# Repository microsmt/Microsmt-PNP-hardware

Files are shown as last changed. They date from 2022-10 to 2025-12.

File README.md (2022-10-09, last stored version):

# Microsmt-PNP-hardwware
# Introduction
  We are building hardware suitable for OPENPNP. All its functions are only for OPENPNP.
# No.1  PNP Mainboard
 1:About the pnp  mainboard The schematic diagram of microsmt pnpboard is modified from the open source document of smoothieboard, mainly as follows:

 2: The network module and temperature measurement module are deleted because they are meaningless to the PNP machine.

 3: The A5984 driver chip is replaced by the easier and cheaper TMC2209 driver module, so the electronic potentiometer MCP4451 is useless. When you need to change the drive current, you need to use a screwdriver to turn the mechanical potentiometer on the TMC2209 module.

4: 3pcs freewheeling diodes is connected in parallel to the drive mos of the vacuum pump and relay. avoid the reverse current of the motor damage the mos.

5: Some chips have been replaced with brands with the same parameters but easier to buy.

6：We do not have a separate software version. It is recommended to obtain the firmware dedicated to OPENPNP from the following link. It is contributed by makr.
                  https://makr.zone/smoothieware-new-firmware-for-pnp/500/
                  
 Notice：The  sch  and  pcb  document   only  open with  AD.
  
# No.2  PNP  Frame
 1： We used aluminum alloy profiles and laser cut aluminum plates to build a low cost but strong framework.The advantage of aluminum cutting piece is that its strength is much higher than that of 3D printing piece, and its accuracy will not be changed due to deformation
 
 2：it  can adjust the height of the platform and the height of feeder  at will,So as to adapt to different lengths of holders.

#  Thank

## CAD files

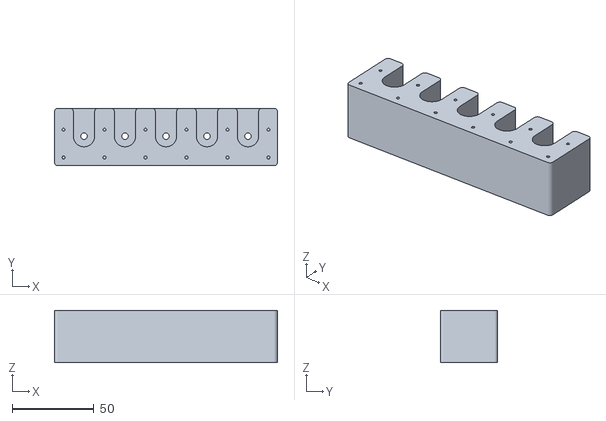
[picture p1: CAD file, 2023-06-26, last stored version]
JUKI -5rack-0625.STL
136.0 x 35.0 x 32.0

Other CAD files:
XX1.DWG

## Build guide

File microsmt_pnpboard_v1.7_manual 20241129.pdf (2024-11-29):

# Microsmt pnpboard v1.7

(2024/11/29)

1: Please check whether the radiator of the drive module contacts the pin.

2: First, use the USB cable to connect the motherboard to the computer. Then

connect the 24VDC with rated current above 15A. The 24VDC input has

reverse connection protection. If you connect the positive and negative poles

reversely, adjust them correctly. carefully study the configuration text in the SD

card, and then try to debug the machine.

3: The TMC2209‘s driver current can be adjusted only when 24V power supply

is used.

4：The TMC2209‘s factory setting is a 32 step subdivision. If you want to

modify it, please refer to the manual of the TMC2209 drive module.

5: Rotate the potentiometer on the | TMC2209‘s | drive module with a

screwdriver to change the reference voltage and adjust the output current,

I=Vref. At this time, the driver is not allowed to connect to the motor.

6: If you use a microsmt PNPv3 machine，No need to adjust the potentiometer,

as we have already set the current at the factory, the current of the

TMC2209‘s drive module as follows: X axis 1.6A, Y axis 1.7A, Z axis 1.0A, N1 axis

0.4A, N2 axis 0.4A.

7: LED 2 and LED 3 flash alternately, indicating that the mainboard is working

normally.

8: When pressing the emergency stop switch, all of stepper motors will stop.

9 : Press RESET or power on again, the config file will be loaded into the

motherboard. The motherboard can work normally only when there is a

config file in the SD card.

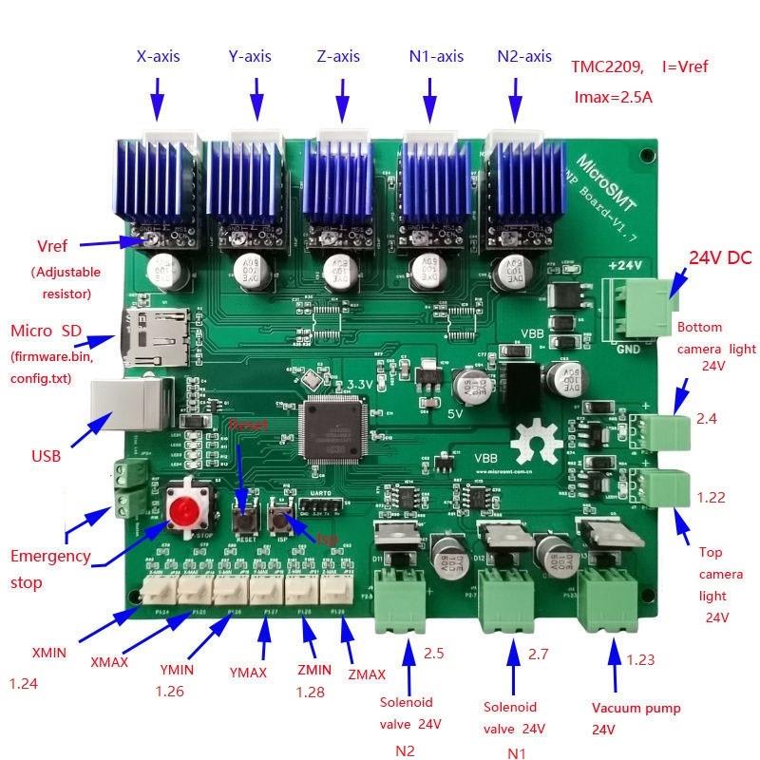
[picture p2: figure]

10 ：Openpnp only needs to configure endstop min, not need endstop

max. All endstop signals are active at high level.

Therefore, the X Y axis uses Omron's SS-5GL switch to trigger the

high level. that is, pin 2 and pin 3 of the Xmin and Ymin are normally closed

to keep low level, when reaching the endstop position, SS-5GL becomes open circuit, pin 3 becomes high level, and endstop action is triggered.

The Z-axis uses Omron's EE-SX672 photoelectric switch to trigger the high

level, You need to query the schematic diagrams of pnpboard v1.7 and EE-

SX672 to understand the connection of the four pins of EE-SX672. First

connect the positive and negative poles of EE-SX672 to pin 1 and pin 2 of

Zmin . Connect OUT to pin 3 of Zmin . Then short-circuit the positive pole of

EE-SX672 and the L pin. This connection mode will enable the OUT pin to

output low level when there is light and output high level when there is no

light, thus triggering Zmin endstop.

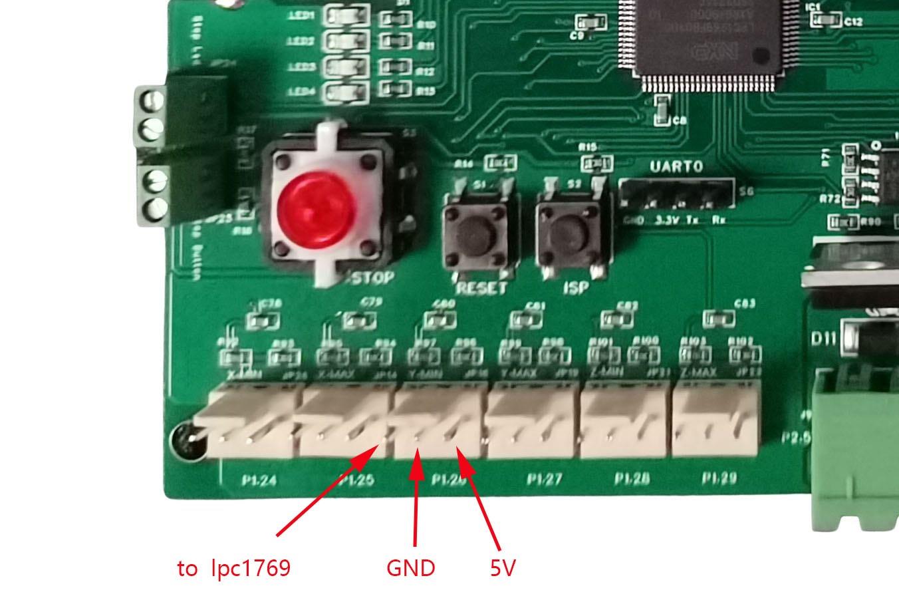
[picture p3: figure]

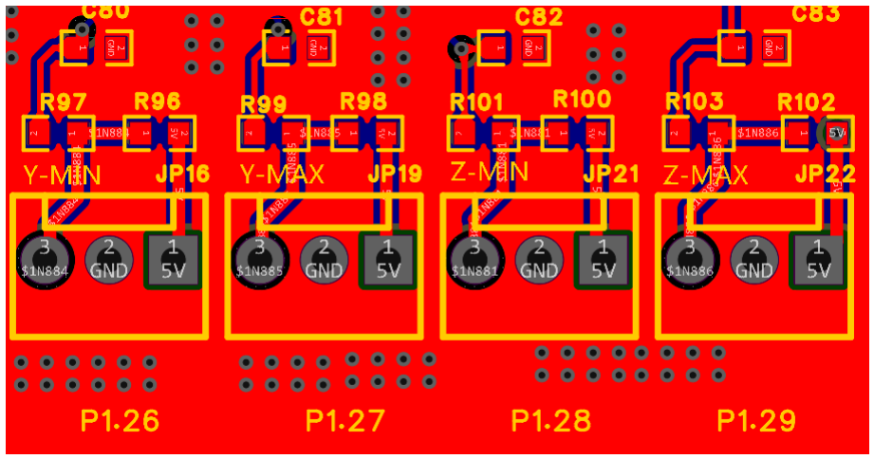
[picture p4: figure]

11 : If you use a microsmt PNPv3 machine, you can directly copy the machine

file to the directory of openpnp2, overwrite the original file, so you don't have to

learn how to configure openpnp from the beginning.

12 : For users of microsmt PNPv3 machine, you can copy the machine.xml file

to the. openpn2 directory on disk C to overwrite the original file, so that you can

run the pnpV3 machine directly. This machine.xml file is generated from the

2023-03-15 version of openpnp software. If you want to use the latest version

of openpnp software, you may need to reset some parameters.

13：Please do not connect the two cameras to the same USB-HUB, because the

data stream is too large and the bandwidth is not enough. You should connect a

camera to your computer separately. The other camera is connected to the

USB-HUB together with the motherboard and feeder control board, and then to

the computer.

14 : Please download the instruction document from this website.

https://github.com/microsmt/Microsmt-PNP-hardware

15 : Please email me if you have any questions microsmtlab@gmail.com.

16 : This motherboard is warranted for 1 year.

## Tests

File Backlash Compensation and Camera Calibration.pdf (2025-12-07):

# Backlash Compensation

# and Camera Calibration

Backlash Compensation and camera calibration are necessary steps. Backlash

Compensation should be completed prior to camera calibration.

### 1. Backlash compensation

Backlash compensation very simple; please refer to OpenPnP's official

manual and video.

https://github.com/openpnp/openpnp/wiki/Backlash-Compensation

https://youtu.be/S5SQE79FWlM

### 2. Camera Lens Calibration

When initializing OpenPnP settings, we need to calibrate the camera lens,

Because the lens has distortion, it needs to be corrected by software.

Video: Initialize openpnp settings on microsmt pnpv3

https://youtu.be/P4USYtvl7yI

. When this video was filmed, we only used one type of camera. Therefore, we

have already completed the lens calibration for users before factory shipment,

so this step does not appear in the Initialize video.

With the increase in camera types, the lens calibration value may be incorrect.

Therefore, if you find the demo board deformed in the camera, you need to re-

perform the lens calibration.

First, print the Calibration Card in the SD card (you can also find it in the link)

and shrink it to fit entirely within the camera's field of view.

https://github.com/microsmt/Microsmt-PNP-hardware/blob/main/Calibration%20card.png

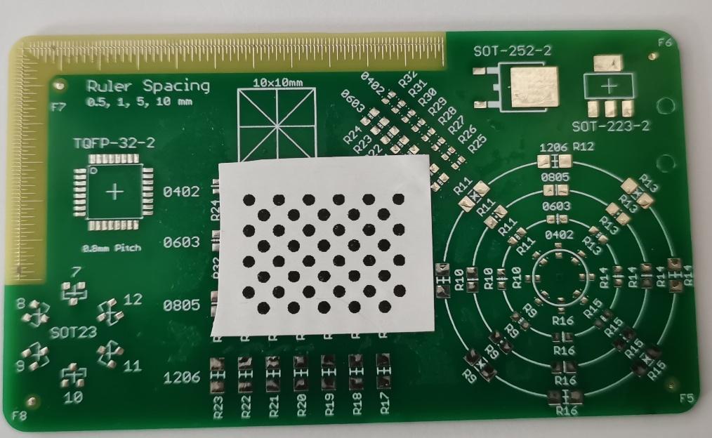
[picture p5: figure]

Then refer to the demonstration video.

Video: Camera Lens Calibration

https://youtu.be/GvGhAD6_fjw

### 3. Advanced Camera Calibration

Manual calibration is a bit cumbersome, so OpenPnP provides a more powerful

advanced calibration function. Let's learn how to use the advanced calibration

function for the top camera.

Refer to the official manual of OpenPnP.

https://github.com/openpnp/openpnp/wiki/Advanced-Camera-Calibration

First, we need to print the new fiducial including the primary fiducial and secondary fiducial. The primary fiducial also serves as the homing fiducial.

The primary fiducial is located on the working plane with a height of Z = -21.

The height difference between the two fiducials is 12, so the height of the

secondary fiducial is Z = -33.

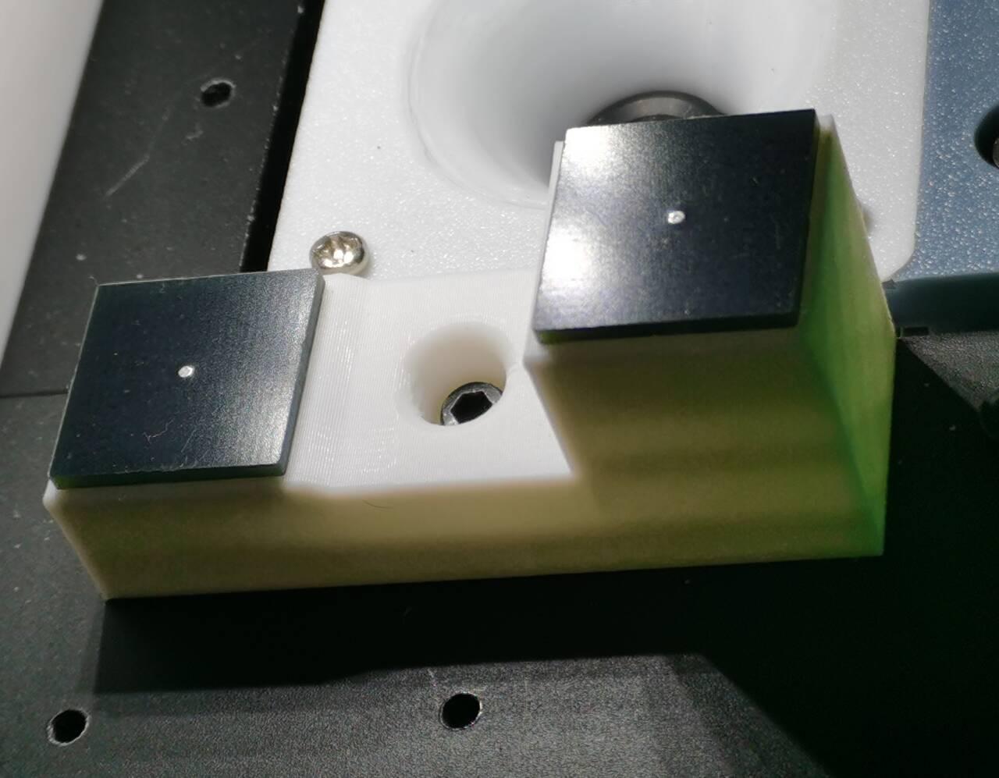
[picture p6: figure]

Refer to the demonstration video.

Video: Advanced calibration for top camera

https://youtu.be/pxEjjD_eYbk

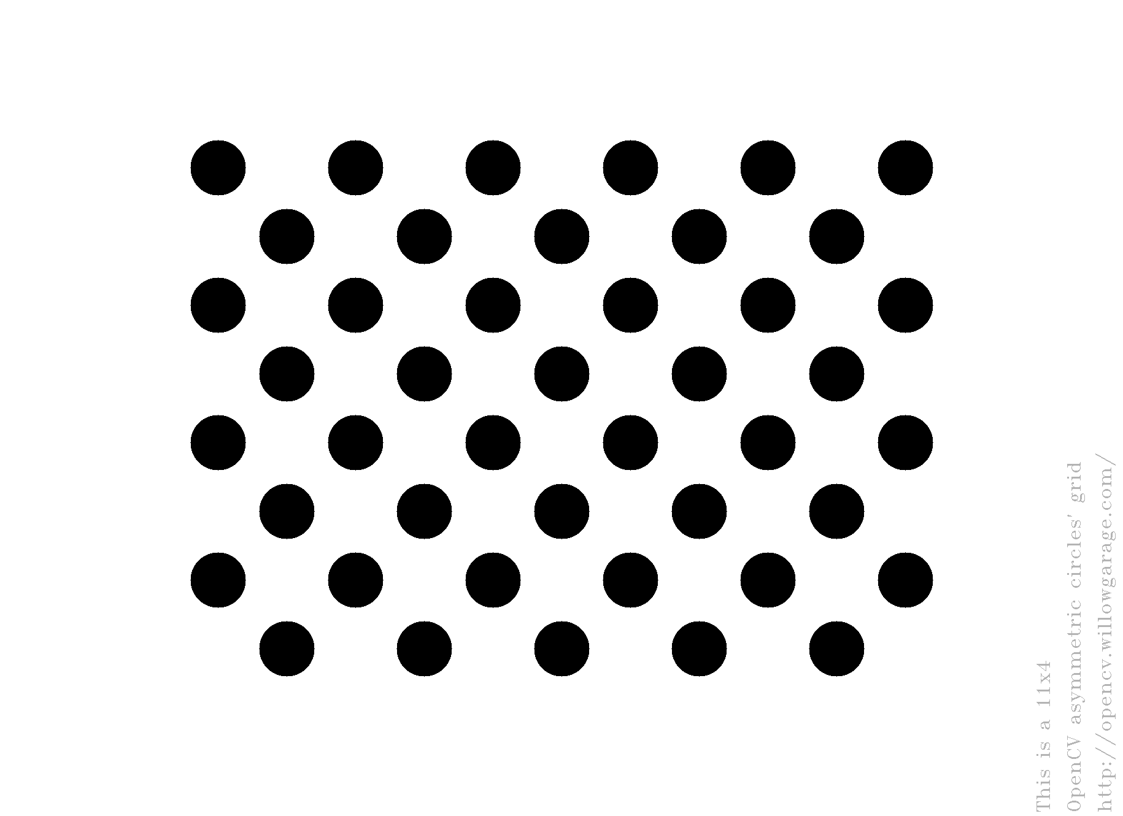
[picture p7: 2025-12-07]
Calibration card.png

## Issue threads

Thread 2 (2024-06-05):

Where is PNP V3 Frame Build Manual?

oOcakemanOo, 2024-06-05:
I do not see the frame assembly manual for the V3 frame anywhere.

microsmt, 2024-06-05:
Based on previous user feedback, they found the document very difficult to
understand and hoped to explain it through video. Therefore, I have taken a
complete installation video, please complete the installation according to
the  follow video .
https://youtu.be/H-nkwTwpxRA

oOcakemanOo ***@***.***> 于2024年6月5日周三 23:38写道：

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

JimDrewGH, 2024-11-26:
While the video good, it is very quick and does not have the same level of detail that your v2.1 (2023-09-06) manual does.  You really need both and a couple of other customer assembly videos to get through the build.

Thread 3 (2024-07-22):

Belt pulley spacers .stl files?

oOcakemanOo, 2024-07-22:
Hello,

I'm using your video to assemble the unit. At 7:45, you install small orange spacers on each side of the belt pulleys.

I don't see those spacers in my kit or in the .stl files, I think. Without those spacers, the carriage the x-axis pulleys rub on the mounting plates. Are those parts I'm missing or am I supposed to print them?

thank you.

microsmt, 2024-07-23:
In the compressed file you downloaded, the 21st STL file is what you mentioned.
---- Replied Message ----
***@***.***>Date7/23/2024 ***@***.***>***@***.***>Subject[microsmt/Microsmt-PNP-hardware] Belt pulley spacers .stl files? (Issue #3)
Hello,
I'm using your video to assemble the unit. At 7:45, you install small orange spacers on each side of the belt pulleys.
I don't see those spacers in my kit or in the .stl files, I think. Without those spacers, the carriage the x-axis pulleys rub on the mounting plates. Are those parts I'm missing or am I supposed to print them?
thank you.
—
Reply to this email directly, view it on GitHub, or unsubscribe.
You are receiving this because you are subscribed to this thread.Message ID: ***@***.***>

JimDrewGH, 2025-04-01:
The belt spacers were made with a huge infill around them (probably to allow better bed adhesion?) so I trimmed that with Solidworks and output the .stl again.

[clip.zip](https://github.com/user-attachments/files/19554812/clip.zip)

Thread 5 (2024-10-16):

0816 body, 3d files invalid?

oOcakemanOo, 2024-10-16:
Hello,

In the 0816 feeder archive downloaded from here.. the 3d files in the "original version" directory open ok in the 3d viewers I have tried, they are all approximately 1.2mb in size.

Your version of the 3d files for the body, however, are all ~250kb in size and none of them open in a couple different 3d viewing software I have tried.

Is there a problem with the files in the archive?

thank you.

microsmt, 2024-10-16:
https://bambulab.com/en-us      I used Bamboo Lab's slicing software to
remove the excess parts from the original 0816 file, and I can also print
it by  Bambu P1.
[image: 1729120882(1).png]   It is a. 3mf file, so it is very small.

The file in GitHub is  no error  , your slicing tool needs to be able to
recognize. 3mf files.

[image: 1729120968(1).png]

oOcakemanOo ***@***.***> 于2024年10月17日周四 05:13写道：

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

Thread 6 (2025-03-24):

Schematic for the motherboard?

noahbliss, 2025-03-24:
Am I able to turn the top camera light on/off via openpnp? I see the open source hardware logo on the motherboard, where are the schematics? Thanks!

JimDrewGH, 2025-05-02:
Yes, you can turn the LED on and off via OpenPnp.  You just click the "light" button that appears in the upper right corner of the camera's display.  You can also manually turn it on and off through the interface.

noahbliss, 2025-05-02:
Thanks @JimDrewGH in this case the mosfet on my specific motherboard was defective. A replacement board fixed this quite expediently!

Closed 2025-05-02.

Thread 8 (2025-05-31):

8mm Worm Motor Support is old version

noeldum, 2025-05-31:
The part called "worm motor support" in 8mm is a rather old version.

It is found under
Bing feeder  3D  file（Magnetic)-0509/Bing  feeder-2mm-4mm-V2（Magnetic)/8-2mm-4mm-feeder- V2(Magnetic）/worm parts/

Could you update github with the newest version?

Or did I look at the wrong place?

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

microsmt, 2025-06-02:
This is correct. It has always been like this without any modifications.
